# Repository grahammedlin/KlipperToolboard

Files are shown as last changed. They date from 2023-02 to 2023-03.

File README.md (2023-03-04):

# Huvud 3D Printer toolhead board USB-PD

A very small 3D printer board for use on a direct drive toolhead. 
It is designed to be used with Klipper firmware.
Klipper has the awesome feature to be able to use multiple MCUs connected to the host over a (relatively) high latency connection. 
This version uses USB-PD instead of CAN. 
Why? USB-C adoption makes premade, robust, and flexible cables capable of supplying power and data generally availabile as commodities.
Also, for fun.
It runs at 20 V instead of 24 V, so maximum fan speed is a little slower. 
24 V is technically possible with USB-PD 3.1 EPR AVS, but the hardware is not commonplace. 

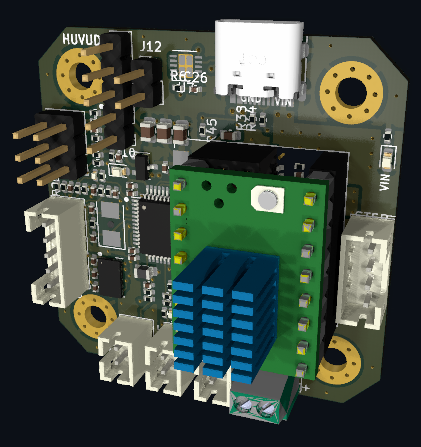
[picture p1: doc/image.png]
Image of Board


---

Based on the amazing work of [bondus](https://github.com/bondus/KlipperToolboard)

Buy it at:

* Lukes Lab: https://lukeslabonline.com/products/huvud
* Tindie: https://www.tindie.com/products/huvud/huvud-3d-printer-hotend-control-board/

Read more about the project activites over at hackaday:
https://hackaday.io/project/174429-huvud-a-3d-printer-tool-head-controller-board

---

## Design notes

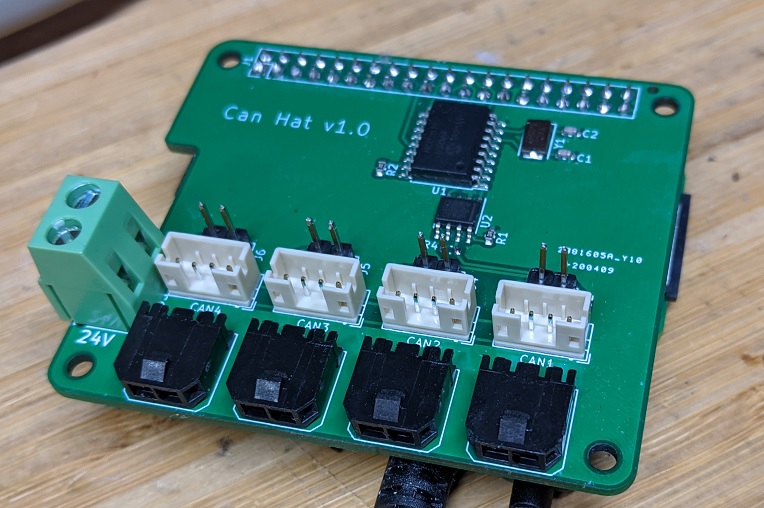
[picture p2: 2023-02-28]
doc/CanHat.jpg

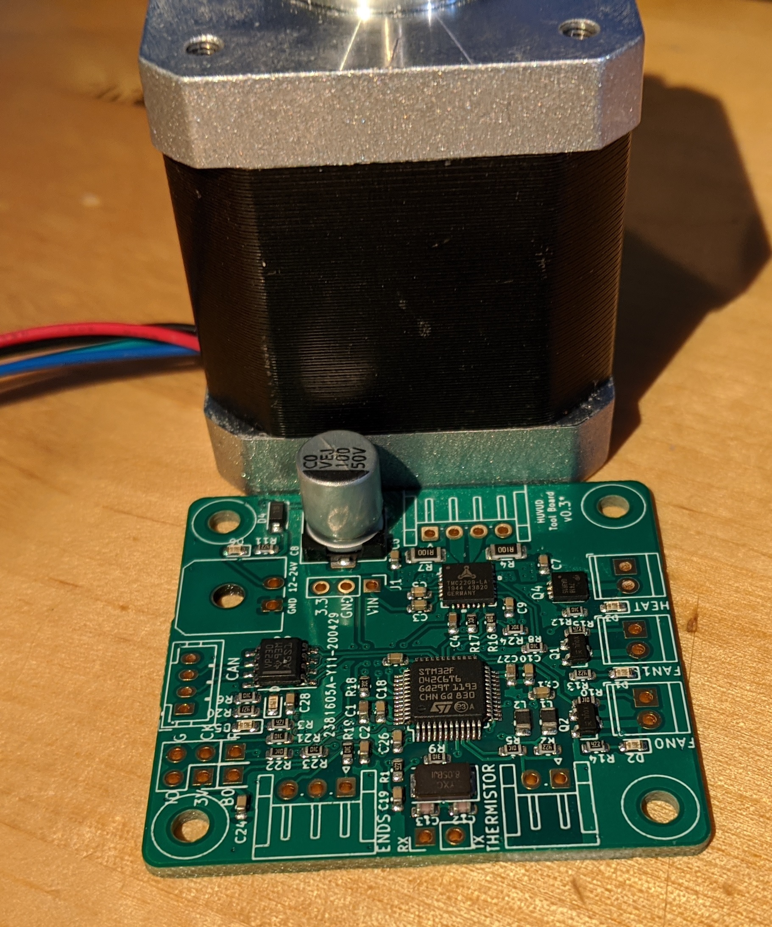
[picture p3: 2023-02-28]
doc/FirstPic.jpg

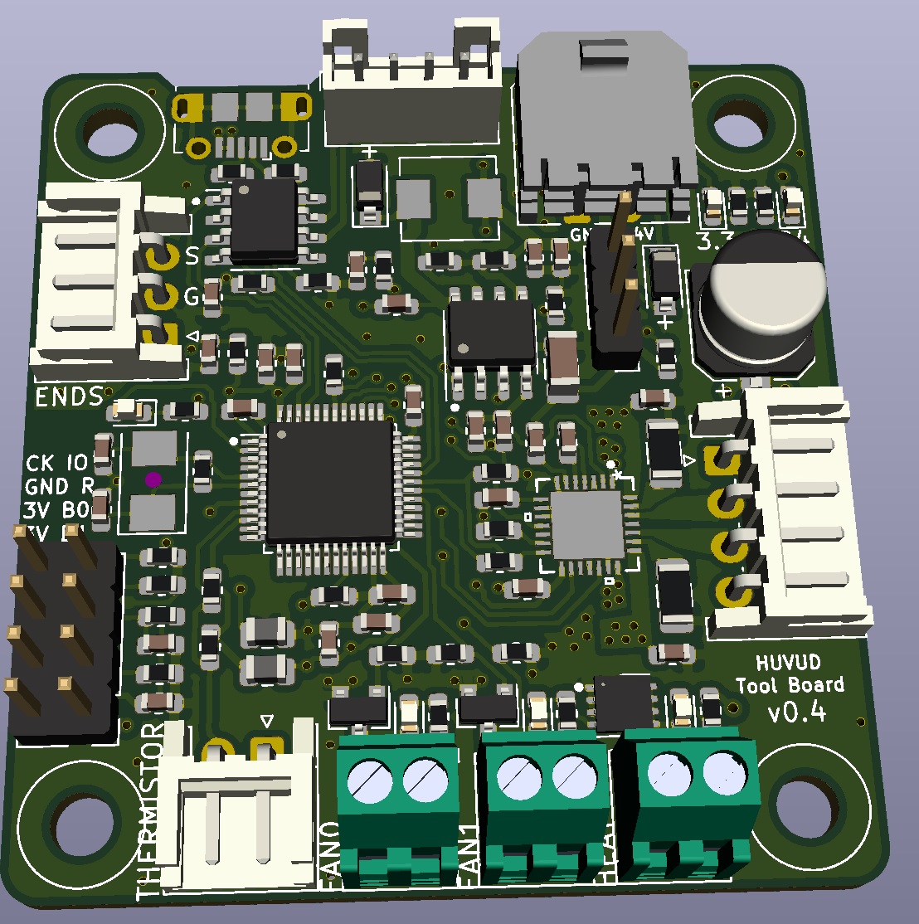
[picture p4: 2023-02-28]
doc/Board.jpg

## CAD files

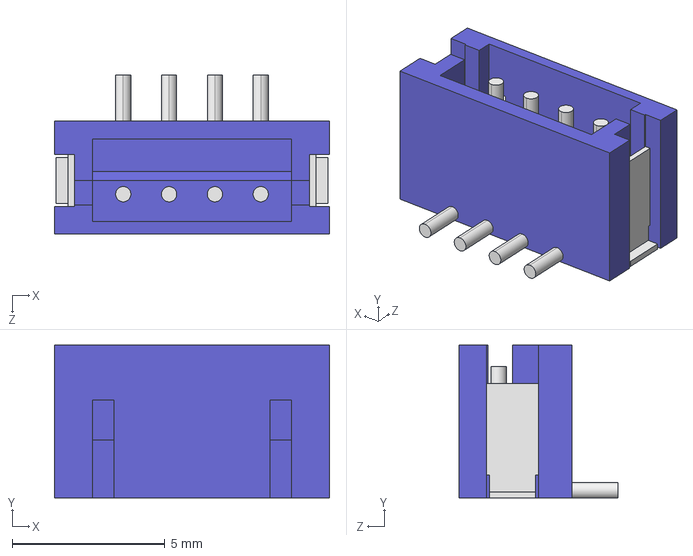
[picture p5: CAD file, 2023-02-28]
3D/B4B-ZR-SM4-TF.STEP
9.00 x 5.00 x 5.20 mm

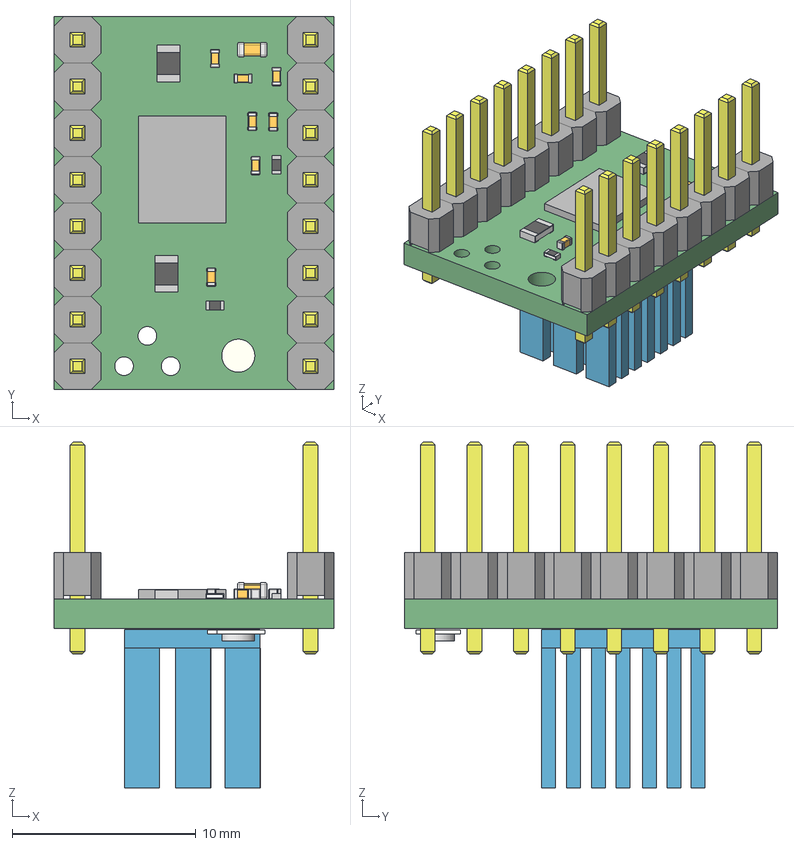
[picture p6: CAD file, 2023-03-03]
TMC2209/tmc2100.step
15.2 x 20.3 x 18.8 mm
Board
1x08 x 4
R0402 x 8
R0805 x 8
C0603 x 2
C0402 x 14
Extruded x 24

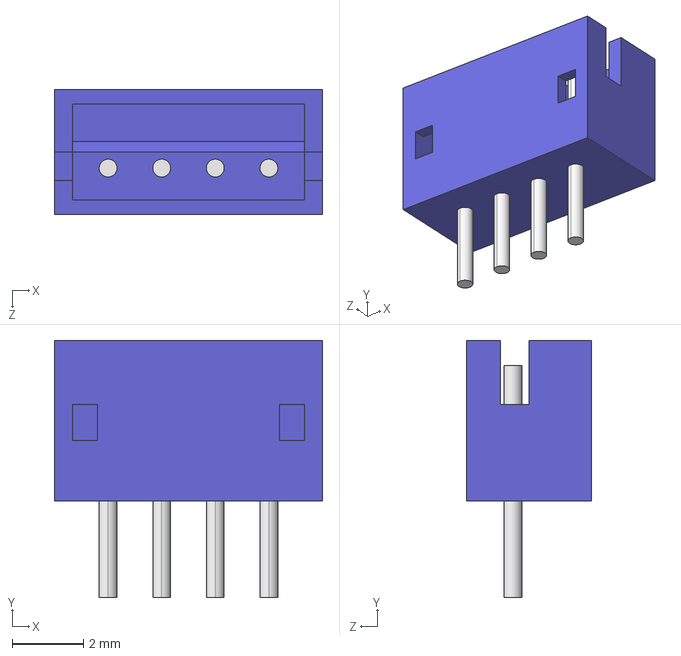
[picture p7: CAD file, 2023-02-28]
3D/B4B-ZR.STEP
7.50 x 7.20 x 3.50 mm

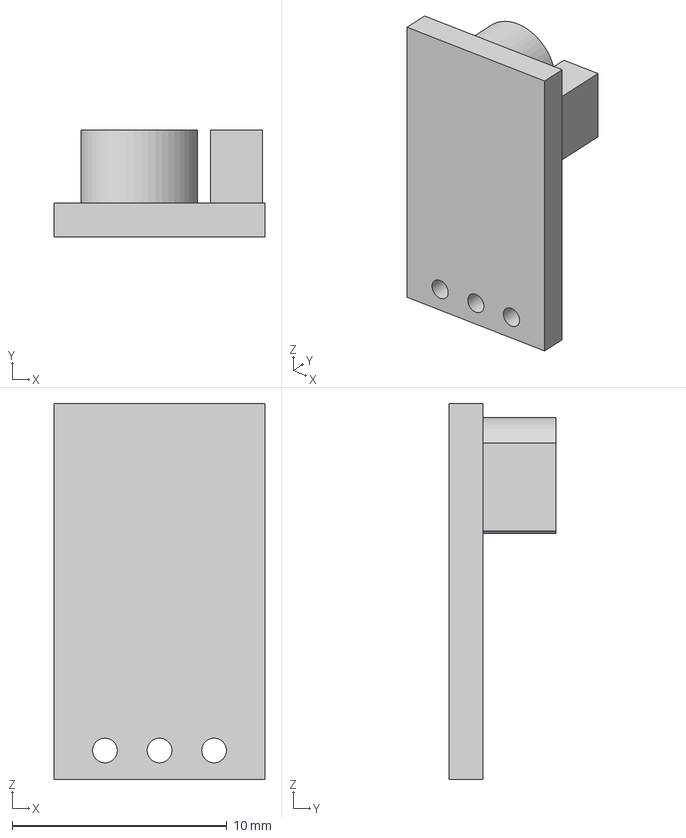
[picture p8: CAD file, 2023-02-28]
3D/Regulator.step
9.80 x 5.00 x 17.5 mm

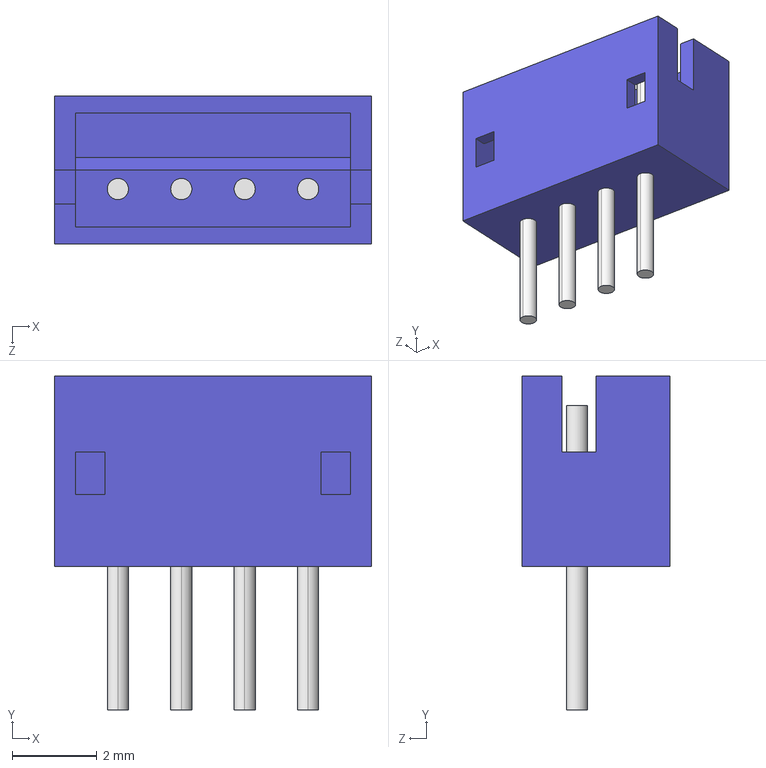
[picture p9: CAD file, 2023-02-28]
3D/B4B-ZR-3.4.STEP
7.50 x 7.90 x 3.50 mm

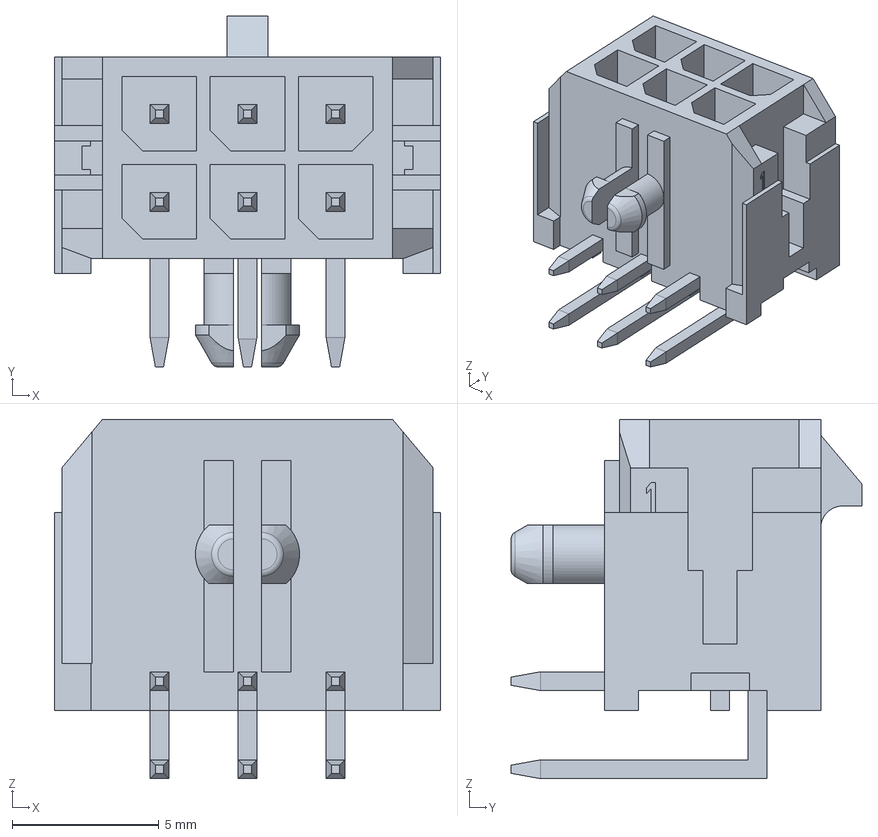
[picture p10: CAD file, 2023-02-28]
3D/molex_430450600.stp
13.2 x 12.0 x 12.2 mm

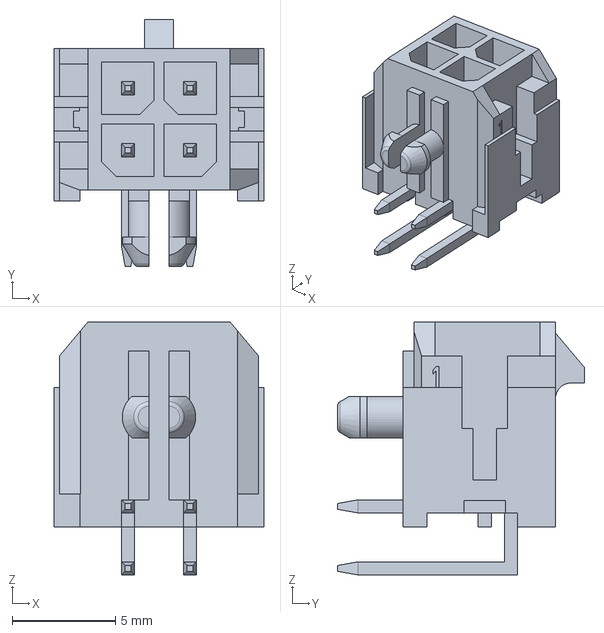
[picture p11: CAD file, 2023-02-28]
3D/molex_430450400.stp
10.1 x 12.0 x 12.2 mm

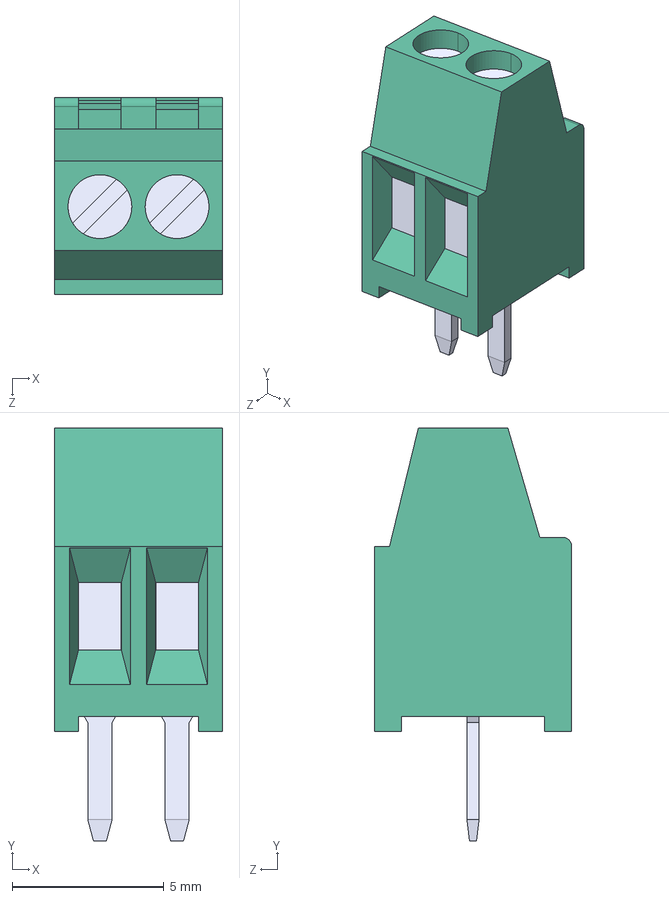
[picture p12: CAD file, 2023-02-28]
3D/TE_282834-2--3DModel-STEP-56544.STEP
5.54 x 13.6 x 6.50 mm

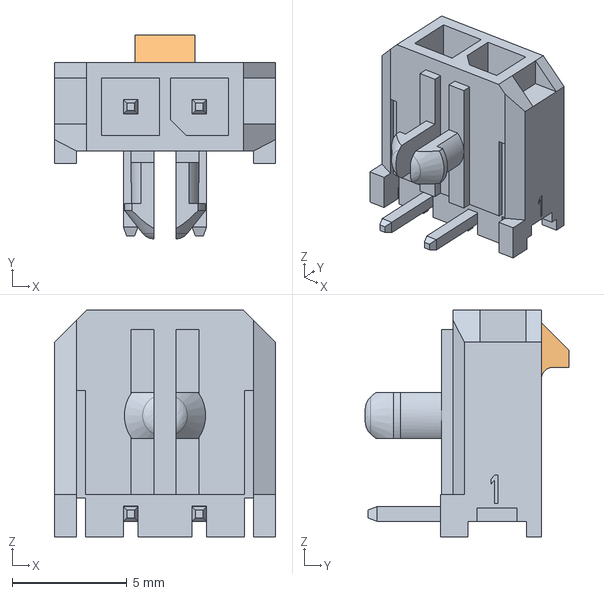
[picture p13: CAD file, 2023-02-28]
3D/molex_436500200.stp
9.65 x 8.90 x 9.90 mm

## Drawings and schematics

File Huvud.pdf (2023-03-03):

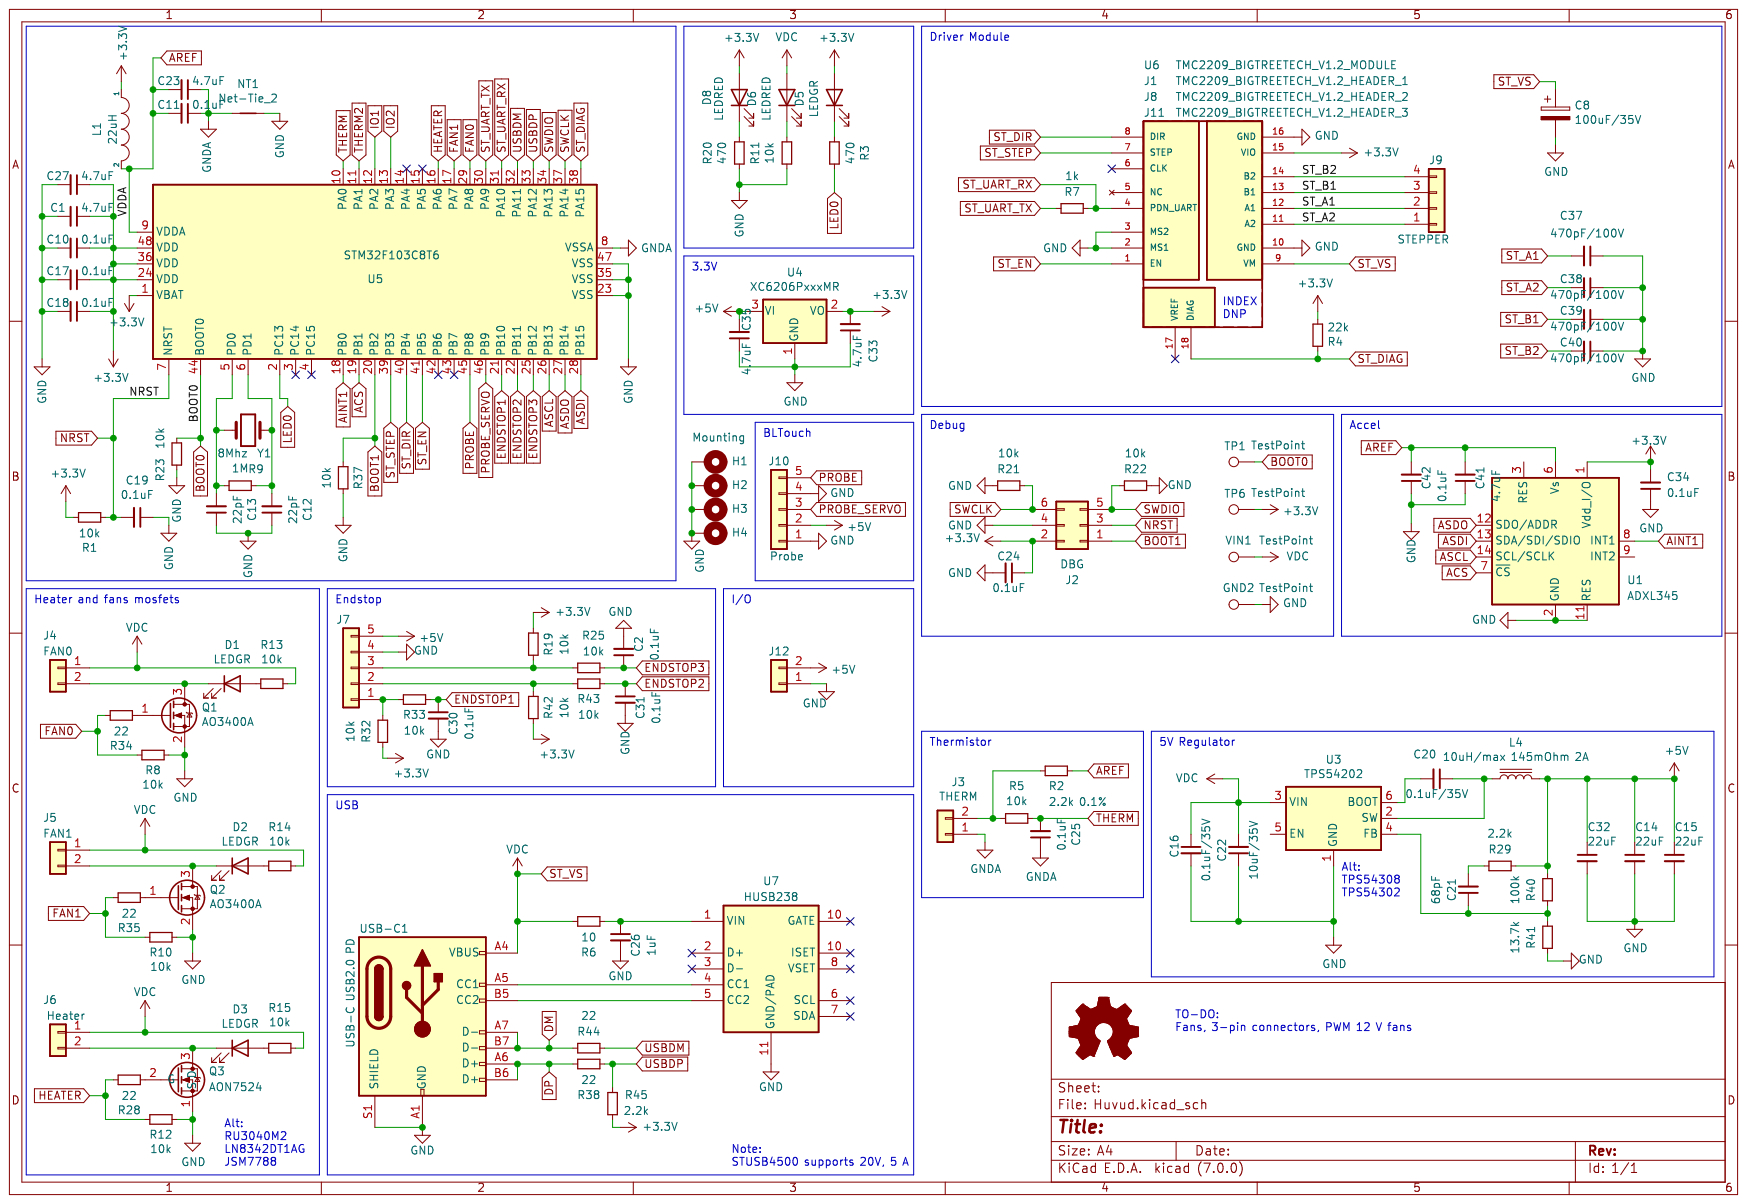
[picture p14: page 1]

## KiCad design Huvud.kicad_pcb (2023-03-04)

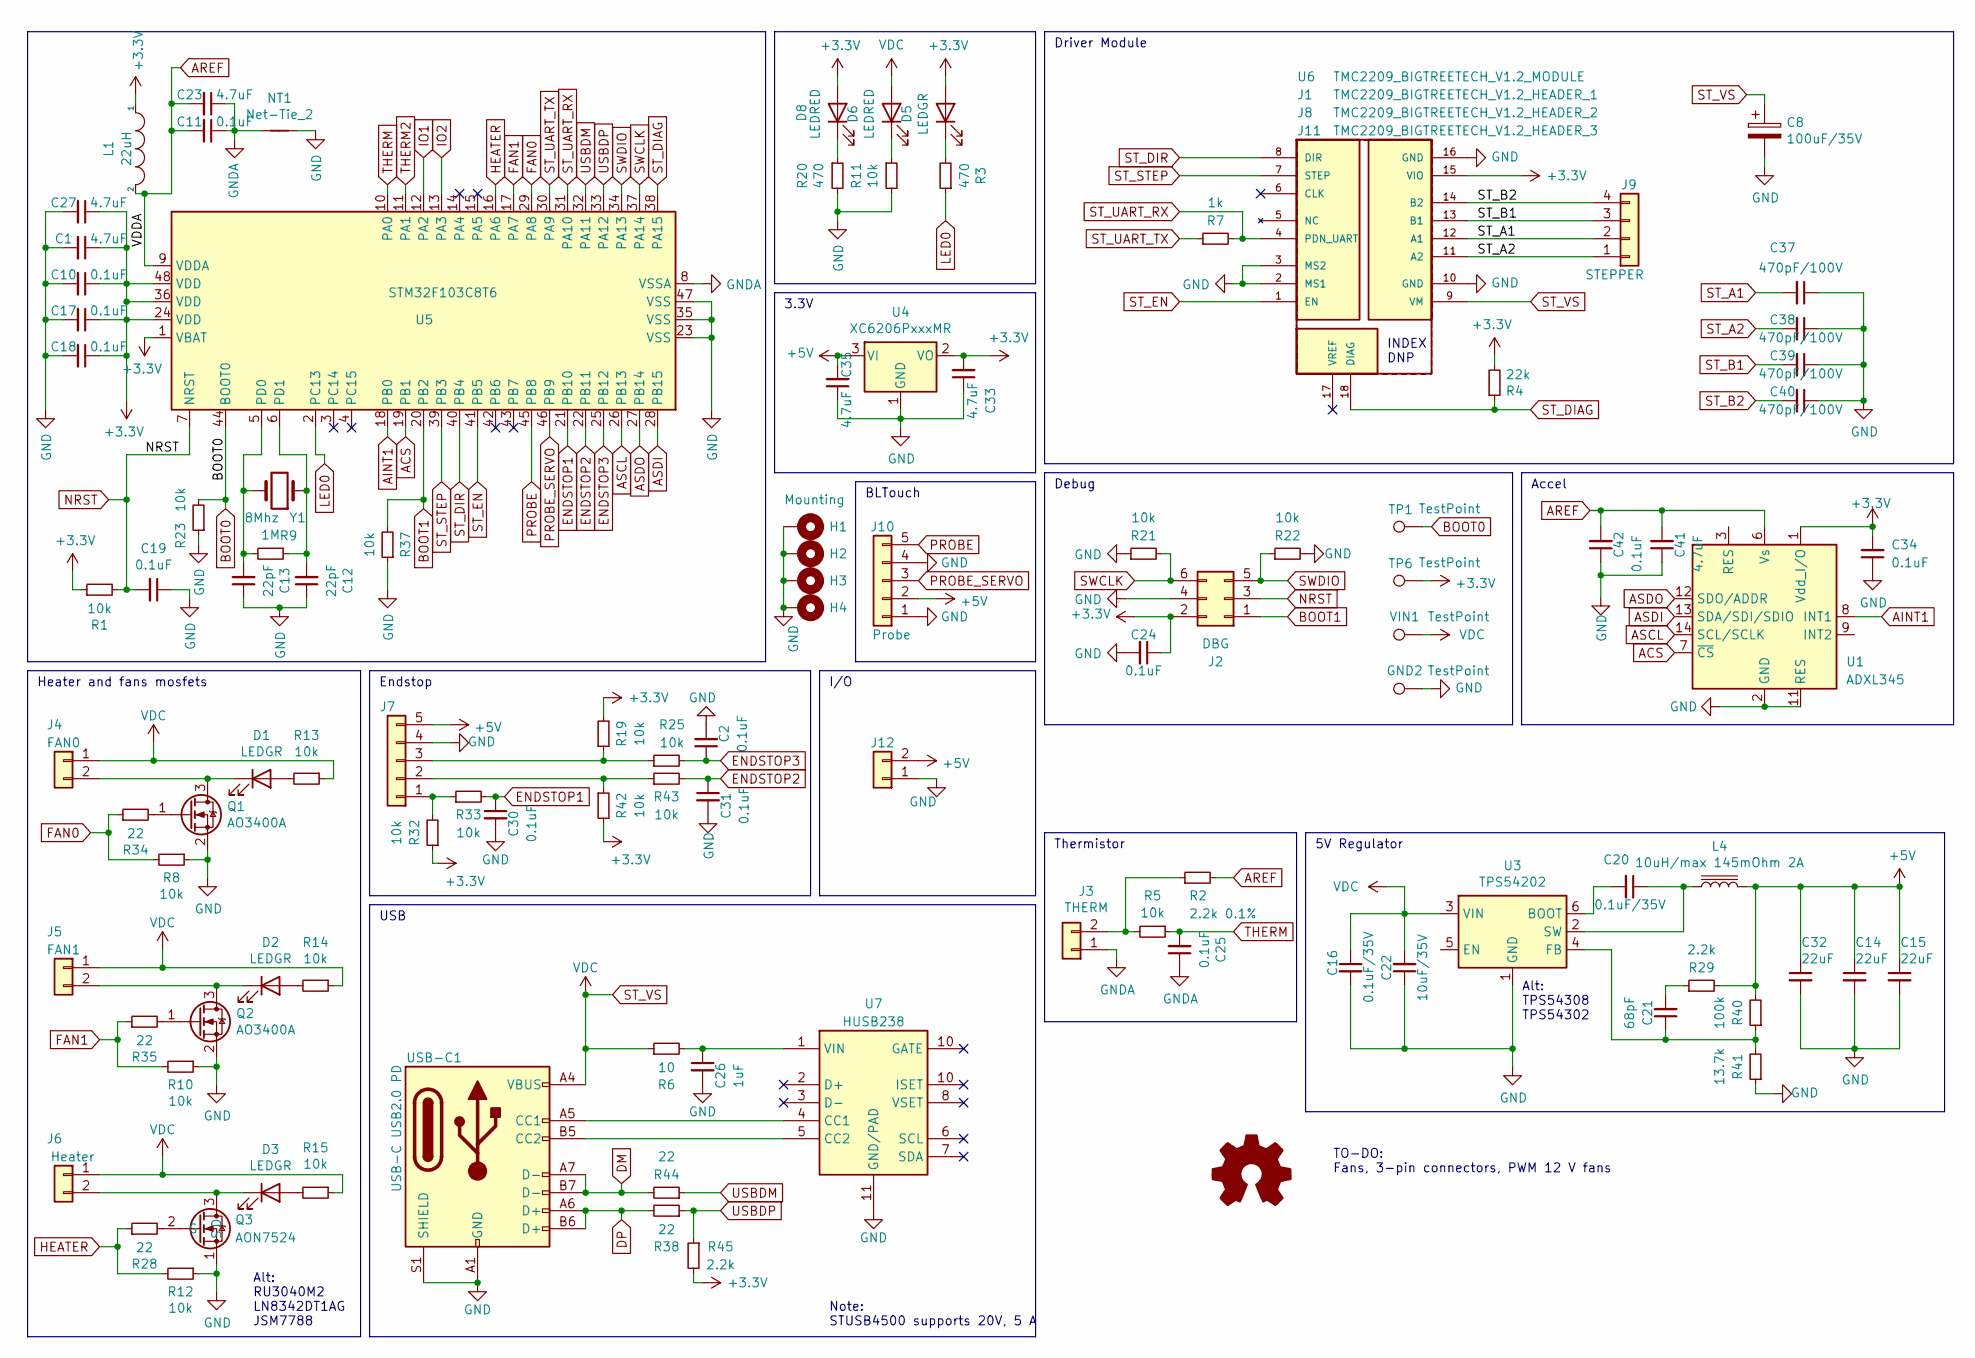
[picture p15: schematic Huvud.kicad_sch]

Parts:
C1, C23, C27, C33, C35, C41: 4.7uF; C_0402_1005Metric; LCSC C23733
C2, C11, C17, C18, C19, C24, C25, C30, C31: 0.1uF; C_0402_1005Metric
C8: 100uF/35V; CP_Elec_6.3x5.8; LCSC C249982
C10, C34, C42: 0.1uF; C_0402_1005Metric; LCSC C1525
C12: 22pF; C_0402_1005Metric; LCSC C1555
C13: 22pF; C_0402_1005Metric
C14, C15, C32: 22uF; C_0805_2012Metric; LCSC C45783
C16, C20: 0.1uF/35V; C_0603_1608Metric; LCSC C14663
C21: 68pF; C_0402_1005Metric; LCSC C14441
C22: 10uF/35V; C_1210_3225Metric; LCSC C13585
C26: 1uF; C_0402_1005Metric
C37, C38, C39, C40: 470pF/100V; C_0603_1608Metric; LCSC C107062
D1, D2, D3, D5: LEDGR; LED_0402_1005Metric; LCSC C74338
D6, D8: LEDRED; LED_0603_1608Metric; LCSC C2286
GND2: TestPoint; TestPoint_Pad_D1.0mm
H1: Mounting; MountingHole_3.2mm_M3_Pad_Via
H2, H3, H4: MountingHole; MountingHole_3.2mm_M3_Pad_Via
J1: TMC2209_BIGTREETECH_V1.2_HEADER_1; HEADER_TMC2209_BIGTREETECH_1
J2: DBG; PinHeader_2x03_P2.54mm_Vertical; LCSC C65114
J3: THERM; JST_PH_B2B-PH-K_1x02_P2.00mm_Vertical; LCSC C2320
J4: FAN0; JST_PH_B2B-PH-K_1x02_P2.00mm_Vertical; LCSC C2319
J5: FAN1; JST_PH_B2B-PH-K_1x02_P2.00mm_Vertical; LCSC C2319
J6: Heater; TerminalBlock_TE_282834-2_1x02_P2.54mm_Horizontal; LCSC C557685
J7: Endstop; JST_PH_B5B-PH-K_1x05_P2.00mm_Vertical; LCSC C2322
J8: TMC2209_BIGTREETECH_V1.2_HEADER_2; HEADER_TMC2209_BIGTREETECH_2
J9: STEPPER; JST_PH_B4B-PH-K_1x04_P2.00mm_Vertical; LCSC C144395
J10: Probe; PinHeader_1x05_P2.54mm_Vertical; LCSC C2322
J11: TMC2209_BIGTREETECH_V1.2_HEADER_3; HEADER_TMC2209_BIGTREETECH_3
J12: 5V; PinHeader_1x02_P2.54mm_Vertical; LCSC C2322
L1: 22uH; L_0805_2012Metric; LCSC C32375
L4: 10uH/max 145mOhm 2A; L_Sunlord_MWSA0518_5.4x5.2mm; LCSC C408412
LOGO1: Logo_Open_Hardware_Small; OSHW-Symbol_6.7x6mm_SilkScreen
NT1: Net-Tie_2; NetTie-2_SMD_Pad0.5mm
Q1, Q2: AO3400A; SOT-23; LCSC C20917
Q3: AON7524; DFN-8-1EP_3x3mm_P0.65mm_EP1.7x2.05mm; LCSC C431195
R1, R5, R8, R10, R12, R13, R14, R15, R21, R23: 10k; R_0402_1005Metric; LCSC C25744
R2: 2.2k 0.1%; R_0402_1005Metric; LCSC C445604
R3, R20: 470; R_0402_1005Metric; LCSC C25117
R4: 22k; R_0402_1005Metric; LCSC C25768
R6: 10; R_0402_1005Metric; LCSC C25744
R7: 1k; R_0402_1005Metric; LCSC C21190
R9: 1M; R_0402_1005Metric; LCSC C26083
R11, R19, R22, R25, R32, R33, R37, R42, R43: 10k; R_0402_1005Metric
R28, R35, R44: 22; R_0402_1005Metric
R29, R45: 2.2k; R_0402_1005Metric; LCSC C25879
R34, R38: 22; R_0402_1005Metric; LCSC C25092
R40: 100k; R_0402_1005Metric; LCSC C25741
R41: 13.7k; R_0402_1005Metric; LCSC C25854
TP1, TP6: TestPoint; TestPoint_Pad_D1.0mm
U1: ADXL345; LGA-14_3x5mm_P0.8mm_LayoutBorder1x6y; LCSC C9667
U3: TPS54202; SOT-23-6; LCSC C191884
U4: XC6206PxxxMR; SOT-23; LCSC C5446
U5: STM32F103C8T6; LQFP-48_7x7mm_P0.5mm; LCSC C8734
U6: TMC2209_BIGTREETECH_V1.2_MODULE; MODULE_TMC2209_BIGTREETECH; PARTREV 1.20
U7: HUSB238; DFN-10-1EP_3x3mm_P0.5mm_EP1.7x2.5mm
USB-C1: USB-C USB2.0 PD; USB_C_Receptacle_GT-USB-7010
VIN1: TestPoint; TestPoint_Pad_D1.0mm
Y1: 8Mhz; Crystal_SMD_5032-2Pin_5.0x3.2mm; LCSC C115962

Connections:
+3V3: C1.1, C10.1, C17.1, C18.1, C24.1, C27.1, C33.2, C34.2, D5.2 (A), D8.2 (A), J2.2, J8.15 (VIO), L1.1, R1.1, R4.2, R19.2, R32.1, R42.2, R45.2, TP6.1, U1.1 (Vdd_I/O), U4.2 (VO), U5.1 (VBAT), U5.24 (VDD), U5.36 (VDD), U5.48 (VDD)
+5V: C14.1, C15.1, C32.1, C35.2, J7.5, J10.2, J12.2, L4.2, R29.2, R40.2, U4.3 (VI)
ACS: U1.7 (~CS), U5.19 (PB1)
AINT1: U1.8 (INT1), U5.18 (PB0)
AREF: C11.2, C23.2, C41.2, C42.2, L1.2, R2.2, U1.6 (Vs), U5.9 (VDDA)
ASCL: U1.14 (SCL/SCLK), U5.26 (PB13)
ASDI: U1.13 (SDA/SDI/SDIO), U5.28 (PB15)
ASDO: U1.12 (SDO/ADDR), U5.27 (PB14)
BOOT0: R23.2, TP1.1, U5.44 (BOOT0)
BOOT1: J2.1, R37.2, U5.20 (PB2)
DM: R44.2, USB-C1.A7 (D-), USB-C1.B7 (D-)
DP: R38.2, USB-C1.A6 (D+), USB-C1.B6 (D+)
ENDSTOP1: C30.1, R33.2, U5.21 (PB10)
ENDSTOP2: C31.1, R43.2, U5.22 (PB11)
ENDSTOP3: C2.1, R25.2, U5.25 (PB12)
FAN0: R8.2, R34.1, U5.29 (PA8)
FAN1: R10.2, R35.1, U5.17 (PA7)
GND: C1.2, C2.2, C8.2, C10.2, C12.1, C13.1, C14.2, C15.2, C16.2, C17.2, C18.2, C19.1, C22.1, C24.2, C26.2, C27.2, C30.2, C31.2, C32.2, C33.1, C34.1, C35.1, C37.1, C38.1, C39.1, C40.1, C41.1, C42.1, GND2.1, H1.1, H2.1, H3.1, H4.1, J1.2 (MS1), J1.3 (MS2), J2.4, J7.4, J8.10 (GND), J8.16 (GND), J10.1, J10.4, J12.1, NT1.1, Q1.2 (S), Q2.2 (S), Q3.1 (S), R8.1, R10.1, R11.2, R12.1, R20.2, R21.1, R22.2, R23.1, R37.1, R41.1, U1.2 (GND), U1.4 (GND), U1.5 (GND), U1.11 (RES), U3.1 (GND), U4.1 (GND), U5.23 (VSS), U5.35 (VSS), U5.47 (VSS), U7.11 (GND/PAD), USB-C1.A1 (GND), USB-C1.A12 (GND), USB-C1.B1 (GND), USB-C1.B12 (GND), USB-C1.S1 (SHIELD)
GNDA: C11.1, C23.1, C25.1, J3.1, NT1.2, U5.8 (VSSA)
HEATER: R12.2, R28.1, U5.16 (PA6)
IO1: U5.12 (PA2)
IO2: U5.13 (PA3)
LED0: R3.1, U5.2 (PC13)
NRST: C19.2, J2.3, R1.2, U5.7 (NRST)
unnamed: C21.2, R29.1
unnamed: D1.2 (A), R13.2
unnamed: D1.1 (K), J4.2, Q1.3 (D)
unnamed: D2.2 (A), R14.2
unnamed: D2.1 (K), J5.2, Q2.3 (D)
unnamed: D3.2 (A), R15.2
unnamed: D3.1 (K), J6.2, Q3.3 (D)
unnamed: D5.1 (K), R3.2
unnamed: D6.1 (K), R11.1
unnamed: D8.1 (K), R20.1
unnamed: J3.2, R2.1, R5.2
unnamed: J7.1, R32.2, R33.1
unnamed: J7.2, R42.1, R43.1
unnamed: J7.3, R19.1, R25.1
unnamed: Q1.1 (G), R34.2
unnamed: Q2.1 (G), R35.2
unnamed: Q3.2 (G), R28.2
unnamed: C20.2, U3.6 (BOOT)
unnamed: C21.1, R40.1, R41.2, U3.4 (FB)
unnamed: C20.1, L4.1, U3.2 (SW)
unnamed: C13.2, R9.2, U5.5 (PD0), Y1.2
unnamed: C12.2, R9.1, U5.6 (PD1), Y1.1
unnamed: U7.4 (CC1), USB-C1.A5 (CC1)
unnamed: U7.5 (CC2), USB-C1.B5 (CC2)
unnamed: C26.1, R6.2, U7.1 (VIN)
PROBE: J10.5, U5.45 (PB8)
PROBE_SERVO: J10.3, U5.46 (PB9)
ST_A1: C37.2, J8.12 (A1), J9.2
ST_A2: C38.2, J8.11 (A2), J9.1
ST_B1: C39.2, J8.13 (B1), J9.3
ST_B2: C40.2, J8.14 (B2), J9.4
ST_DIAG: J11.18 (DIAG), R4.1, U5.38 (PA15)
ST_DIR: J1.8 (DIR), U5.40 (PB4)
ST_EN: J1.1 (EN), U5.41 (PB5)
ST_STEP: J1.7 (STEP), U5.39 (PB3)
ST_UART_RX: J1.4 (PDN_UART), R7.2, U5.31 (PA10)
ST_UART_TX: R7.1, U5.30 (PA9)
ST_VS: C8.1, C16.1, C22.2, D6.2 (A), J4.1, J5.1, J6.1, J8.9 (VM), R6.1, R13.1, R14.1, R15.1, U3.3 (VIN), USB-C1.A4 (VBUS), USB-C1.A9 (VBUS), USB-C1.B4 (VBUS), USB-C1.B9 (VBUS), VIN1.1
SWCLK: J2.6, R21.2, U5.37 (PA14)
SWDIO: J2.5, R22.1, U5.34 (PA13)
THERM: C25.2, R5.1, U5.10 (PA0)
THERM2: U5.11 (PA1)
USBDM: R44.1, U5.32 (PA11)
USBDP: R38.1, R45.1, U5.33 (PA12)

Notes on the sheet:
3.3V
5V Regulator
Endstop
I/O
Debug
Note: STUSB4500 supports 20V, 5 A
Driver Module
TO-DO: Fans, 3-pin connectors, PWM 12 V fans
Alt: RU3040M2 LN8342DT1AG JSM7788
Thermistor
Heater and fans mosfets
USB
Accel
Alt: TPS54308 TPS54302
BLTouch
INDEX DNP

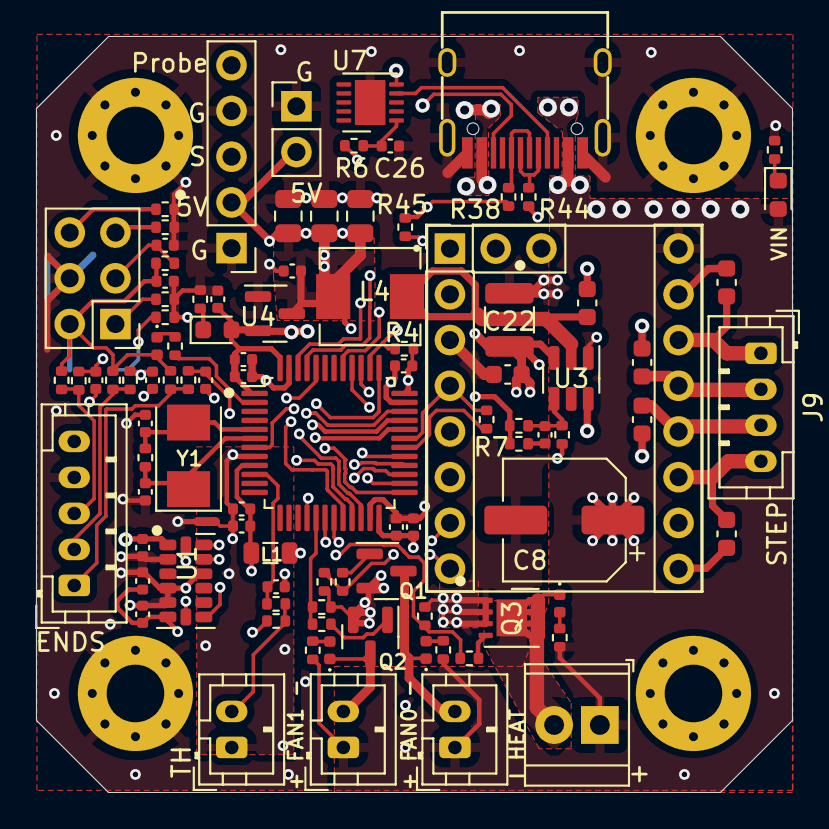
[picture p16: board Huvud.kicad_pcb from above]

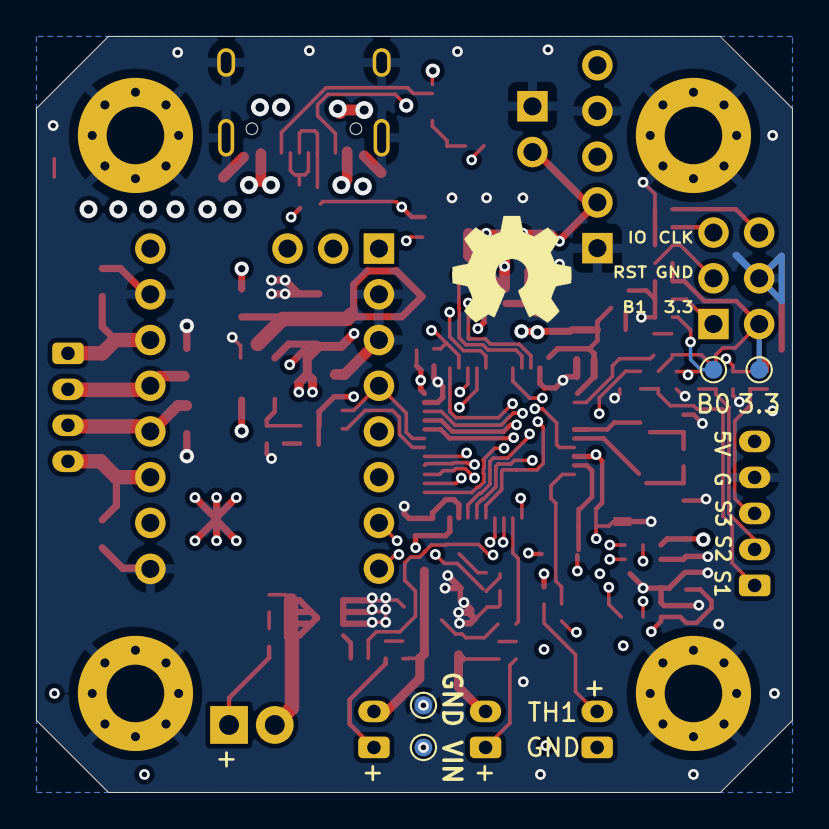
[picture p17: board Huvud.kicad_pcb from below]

Board: 4 copper layers, 42.0 x 42.0 mm, 109 parts (5 on the bottom side), 65 nets.

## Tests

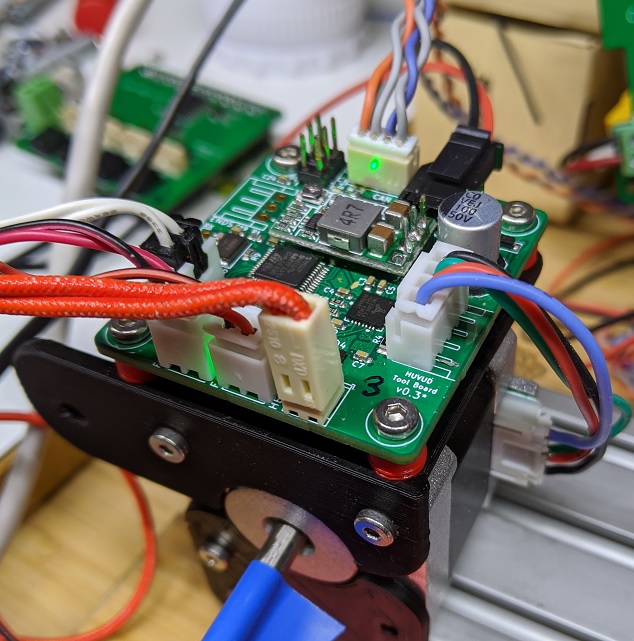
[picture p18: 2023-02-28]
doc/TestSetup.jpg

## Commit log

2023-02-28 replace CAN with USB-C PD, remove other version
    [48037-0001.step, B4B-ZR-3.4.STEP, B4B-ZR-SM4-TF.STEP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]
2023-03-03 repace TMC2209 with module
    [Huvud.kicad_pcb, Huvud.kicad_sch, tmc2100.step]
2023-03-04 cleanup and bom
    [Huvud.kicad_pcb, Huvud.kicad_sch]

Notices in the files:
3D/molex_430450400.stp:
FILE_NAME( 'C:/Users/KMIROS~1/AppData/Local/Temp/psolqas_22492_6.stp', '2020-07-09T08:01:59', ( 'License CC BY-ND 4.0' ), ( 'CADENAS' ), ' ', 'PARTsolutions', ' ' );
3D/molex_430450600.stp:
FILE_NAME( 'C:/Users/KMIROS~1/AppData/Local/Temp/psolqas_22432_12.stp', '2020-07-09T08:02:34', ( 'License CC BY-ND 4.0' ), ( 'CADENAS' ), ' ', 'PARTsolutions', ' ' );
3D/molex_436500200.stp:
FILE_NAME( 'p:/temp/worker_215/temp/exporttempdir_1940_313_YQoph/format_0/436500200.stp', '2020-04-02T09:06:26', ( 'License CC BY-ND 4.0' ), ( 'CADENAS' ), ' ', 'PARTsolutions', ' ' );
